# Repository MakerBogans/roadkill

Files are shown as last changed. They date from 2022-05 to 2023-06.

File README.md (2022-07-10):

<div style="text-align: right"><sub>A MakerBogans & Safflower Production</sub></div>


# Roadkill Enhanced Toolhead PCB Family

The RKE family of toolhead boards are based off the roadkill board designed xbst\_ but offers numerous improvements.

- Heater current capacity is greatly improved offering 5A of capacity on the RKE-Long board and 6A on RKE<sup>2</sup>.
- Support for simultaneous use of neopixels, filament sensor, inductive probe and x endstop switch with dedicated ports for all features.
- All boards within the RKE family are pin compatible allowing for mix and matching of boards.

<p align="middle" >
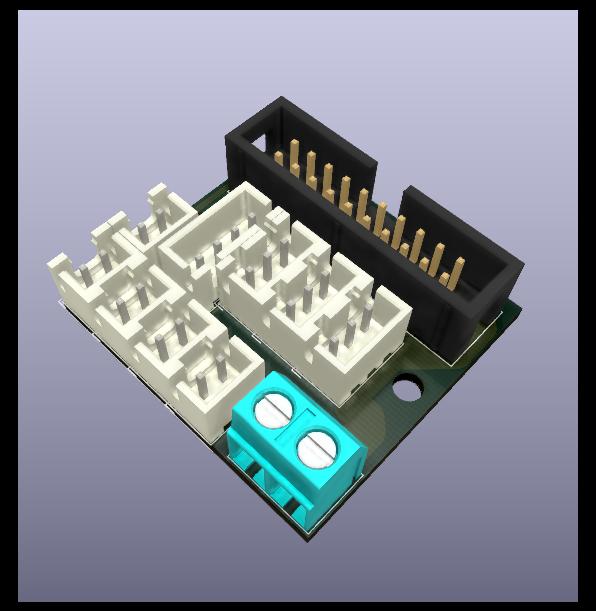
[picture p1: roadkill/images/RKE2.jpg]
  
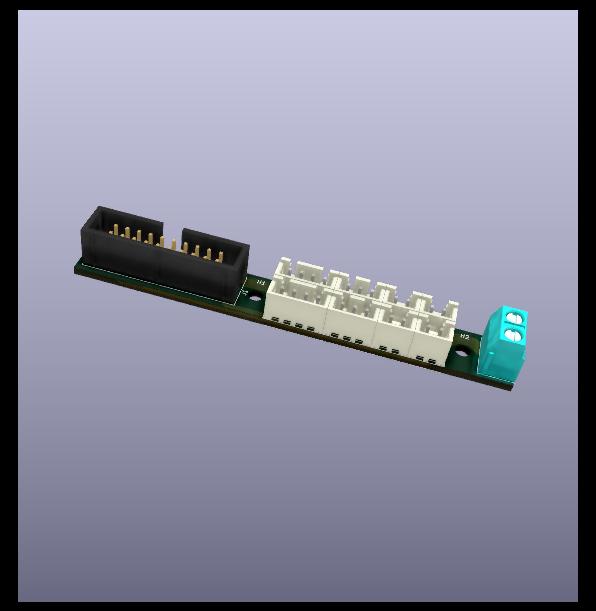
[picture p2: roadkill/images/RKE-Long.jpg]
   
</p>

## Important Notes

- Heater screw terminal is polarised, as the 24V supply is used as a common rail.
- Nylon or printed washers should be used to protect the mounting holes due to the proximity of the traces to the holes.
- LED port is designed for neopixels and uses a common 5V rail with the filament sensor port.
- Probe port has a 24V power rail derived from the heater.

&#9888;<b>Do not connect a wire between the MCU and the Roadkill probe port for V, this will result in backfeeding 24V into the MCU. V is provided from the Heater</b>

## BOM

Per Board,

- 1 x 20 pin IDC header (2x10 2.54mm pitch)
- 5 x 2 pin JST-XH
- 3 x 3 pin JST-XH (2x for RKE Long)
- 1 x 4 pin JST-XH (2X for RKE Long)
- 1 x 5 mm pitch screw terminal (TB00250002BE)

Molex temp-flex ribbon is the preferred ribbon solution (Molex, 100057-0101).

For IDC connector/sockets 3M D89120-0131HK with D3448-89120 strain relief clip are the preferred solutions.

## Pinout for Ports

IDC numbering is ODD_EVEN with 1 denoted by an arrow on the PCB

Pin 1 of the JST-XH ports is the square pads on the PCB.

For RKE<sup>2</sup>

| Port | Pin 1 (IDC PIN)  | Pin 2 (IDC PIN) | Pin 3 (IDC PIN) | Pin 4 (IDC PIN) |
| --- | --- | --- | --- | --- |
| Layer Fan | Fan Voltage (18) | Fan GND (20) | - | - |
| Heater Fan | Fan Voltage (14) | Fan GND (16) | - | - |
| X endstop | GND (2) | Signal (12) | - | - |
| Filament Sensor  | 5 V (4) | GND (2) | Signal (10) | - |
| Neopixel | 5 V (4) | GND (2) | Data In (6) | - |
| Probe | 24 (1,2) | GND (2) | Signal (8) | - |
| Thermistor (T0)  | T0 (11) | GNDA (9) | - | - |
| Extruder Stepper | A1 (19) | A2 (17) | B1 (15) | B2 (13) |
| Heater | 24 V (1,3) | HE GND (5,7) | - | - |

RKE Long utilises a combined Filament Sensor and X endstop port pinout is below.

| Port | Pin 1 (IDC PIN) | Pin 2 (IDC PIN) | Pin 3 (IDC PIN) | Pin 4 (IDC PIN) |
| --- | --- | --- | --- | --- |
| Combined FS and XES | 5 V (4) | GND (2) | Signal (12) | Signal (10) |

# Schematic

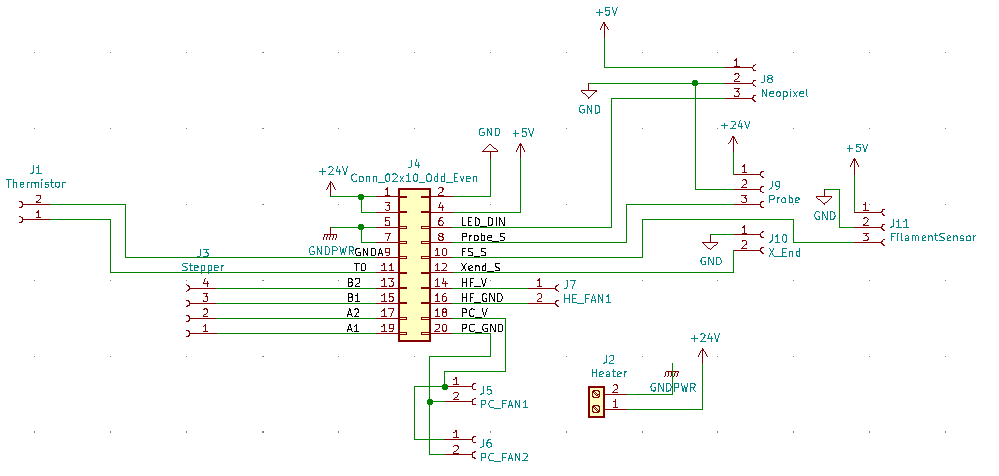
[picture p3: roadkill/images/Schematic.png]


# Probe Wiring
It is critical to wire Z probe correctly to avoid damage to MCU. Follow the below wiring guides

|  |  |
| --- | --- |
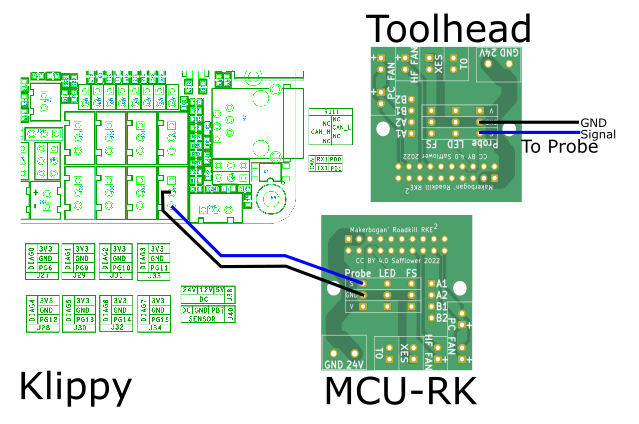
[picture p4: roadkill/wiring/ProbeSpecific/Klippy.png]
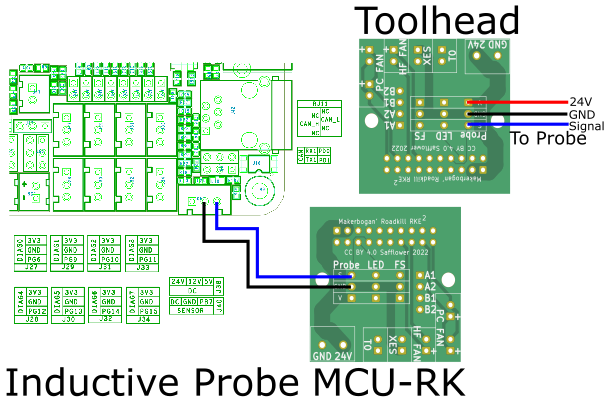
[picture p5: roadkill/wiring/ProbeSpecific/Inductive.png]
|   |  |
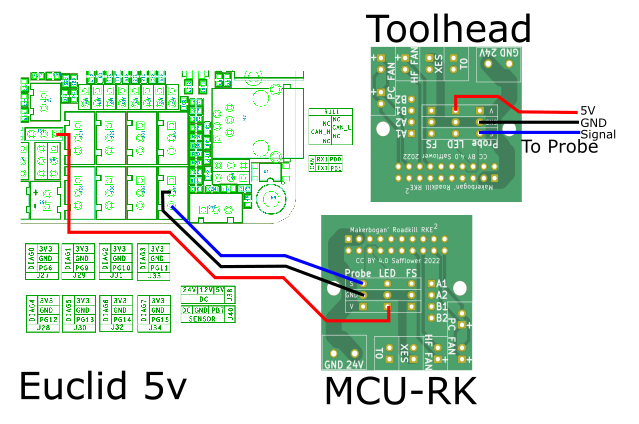
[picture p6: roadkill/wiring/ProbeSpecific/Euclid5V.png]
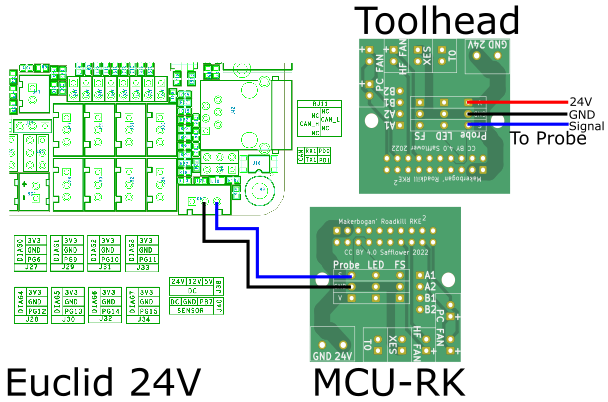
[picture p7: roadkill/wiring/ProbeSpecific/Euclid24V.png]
| |   |

# Troubleshooting

| Number | Symptoms | Cause | Solution |
|---| --- | --- | --- |
| 1 | X endstop is permently triggered or not triggering | X end stop is shorted to GND on the MCU->Roadkill board, S is connected to G on the X endstop port  | Swap X endstop pins on the MCU->Roadkill board |
| 2 | Probe disconnecting when heater is turned  on, Flickering Probe during PWM control of the Probe | Reversed Polarity on the 24 V Screw terminal on the MCU->Roadkill board | Swap  Heater Wires on the MCU->Roadkill board |

# License

<br />This work is licensed under a <a rel="license" href="http://creativecommons.org/licenses/by/4.0/">Creative Commons Attribution 4.0 International License</a>.

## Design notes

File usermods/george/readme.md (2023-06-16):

# Mod description

Another take on the RKE Square mount for the a drive.

Use the pinned version if you have the pinned mod for an easier print.

Can get to the motor mount bolts with use of creative angles.

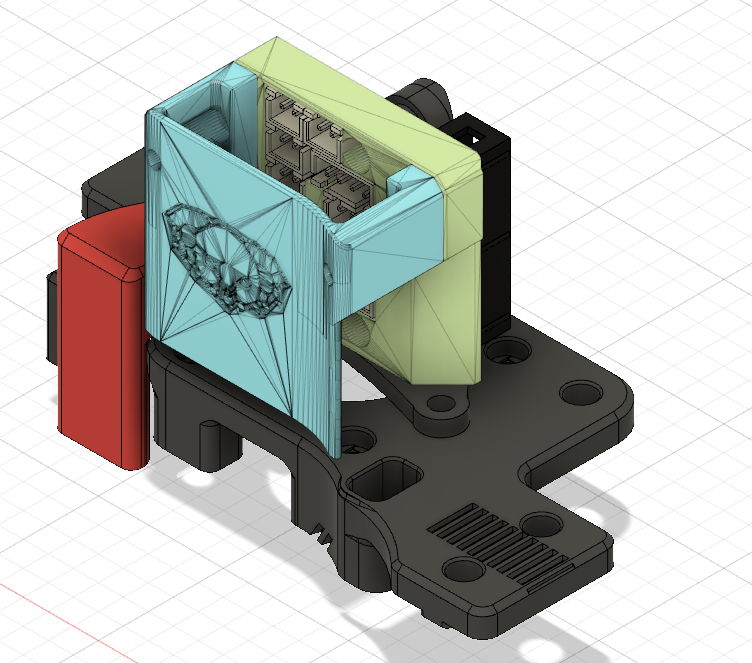
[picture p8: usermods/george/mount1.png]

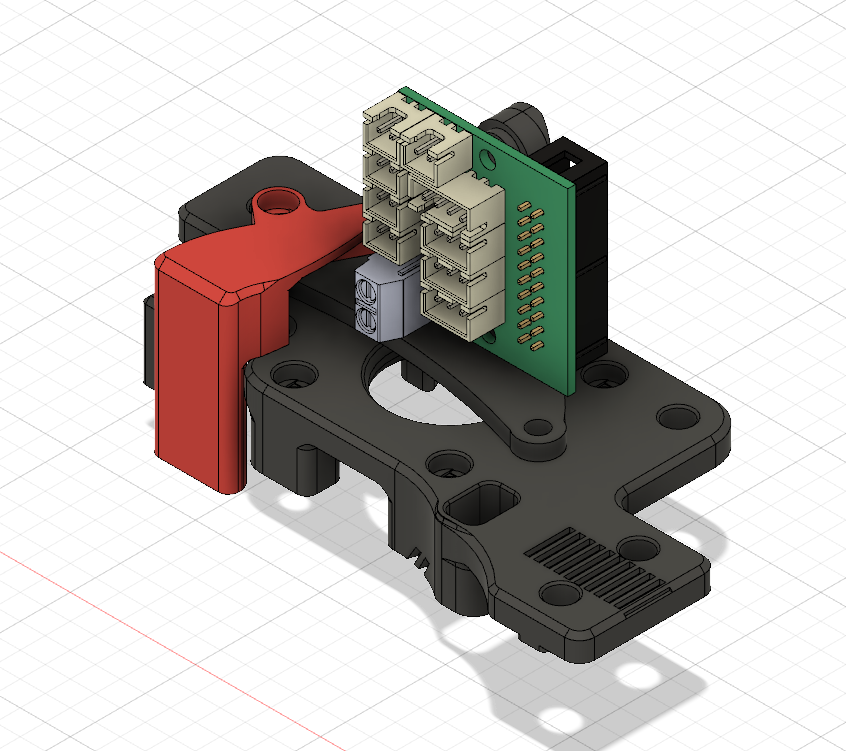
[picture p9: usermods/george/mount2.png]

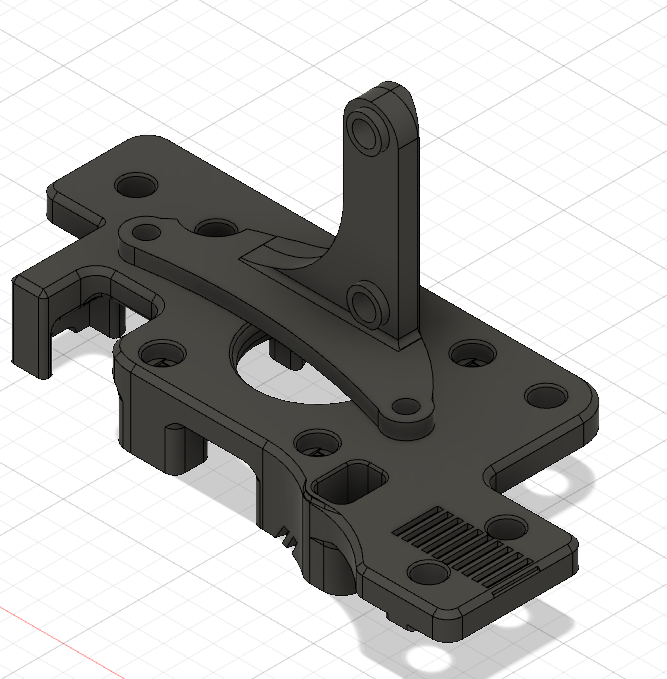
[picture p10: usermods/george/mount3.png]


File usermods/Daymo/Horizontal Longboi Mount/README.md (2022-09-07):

<div style="text-align: right"><sub>A MakerBogans Production</sub></div>


# Horizontal Gantry Mount for RKE Longboi

This mount allows you to use an RKE Longboi on your gantry!

<p align="middle" >
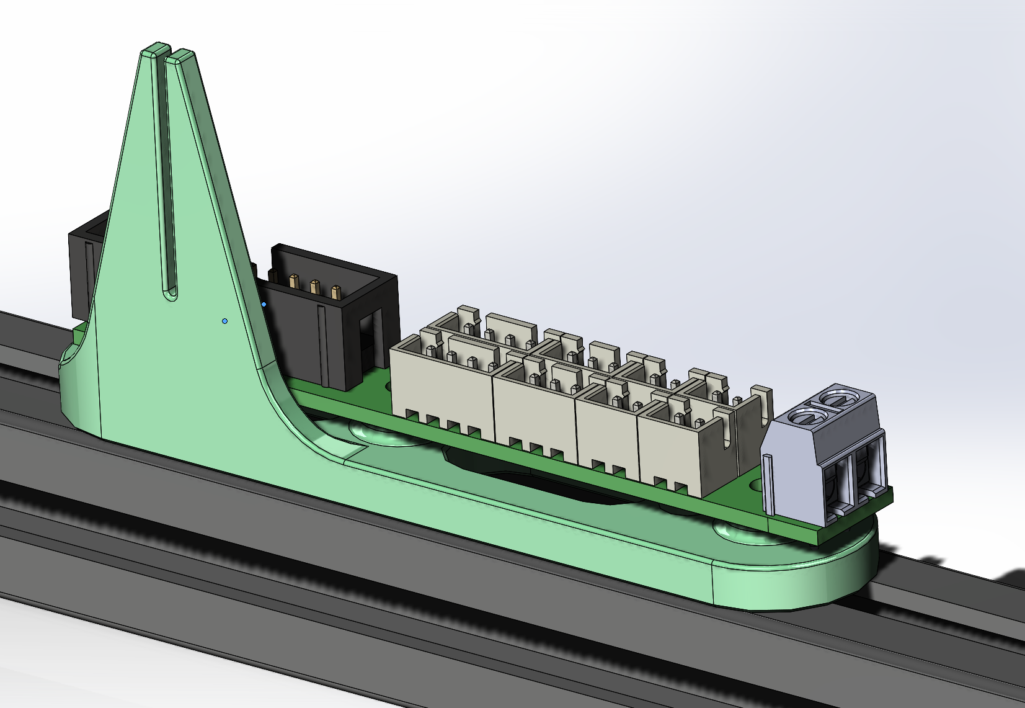
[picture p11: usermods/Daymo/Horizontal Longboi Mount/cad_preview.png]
  
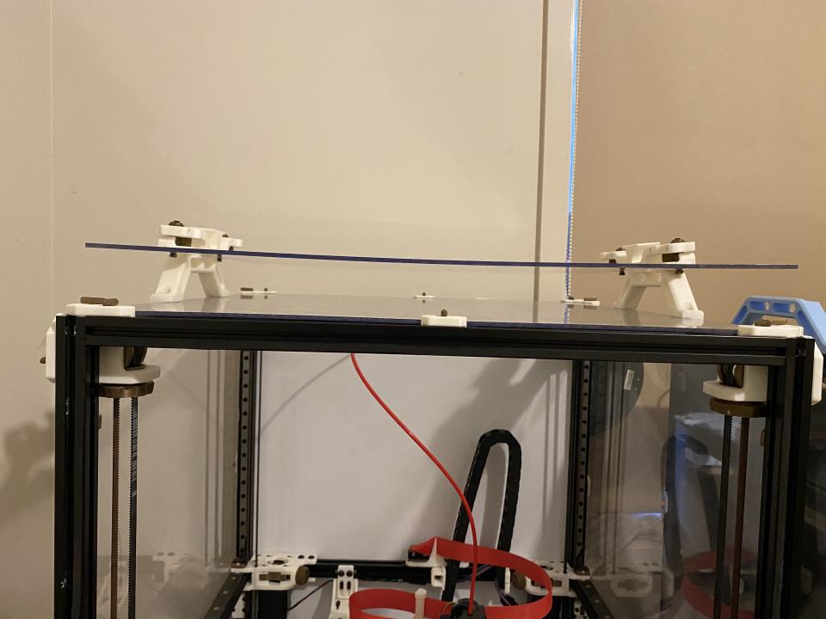
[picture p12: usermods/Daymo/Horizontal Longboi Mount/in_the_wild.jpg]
   
</p>

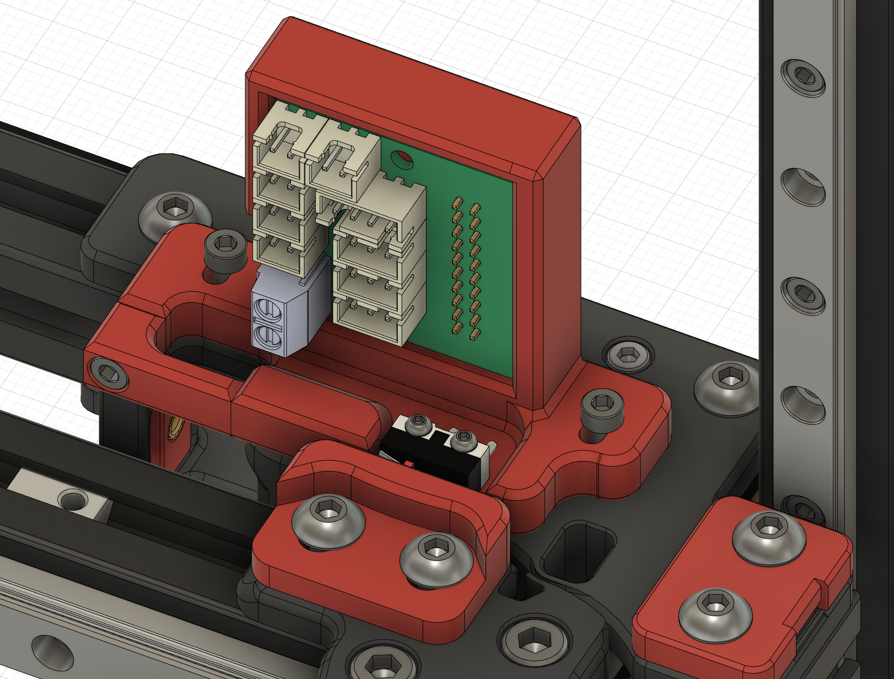
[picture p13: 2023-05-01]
usermods/RedGT500/RKE V2.4 Rear Mount (No Pins Mod)/Pictures/RKE_Mount_05.png

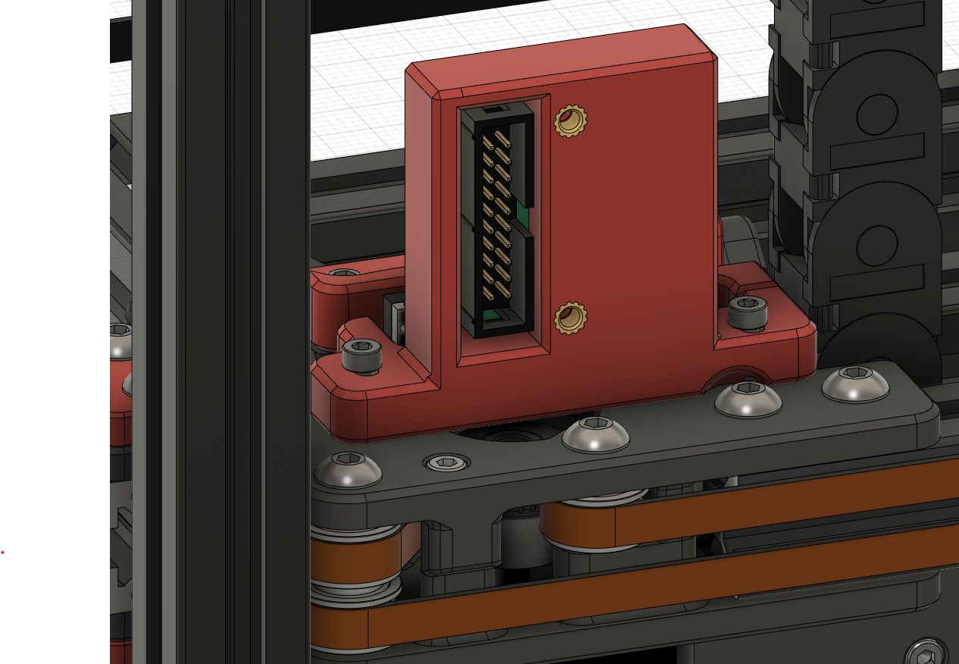
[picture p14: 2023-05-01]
usermods/RedGT500/RKE V2.4 Rear Mount (No Pins Mod)/Pictures/RKE_Mount_03.png

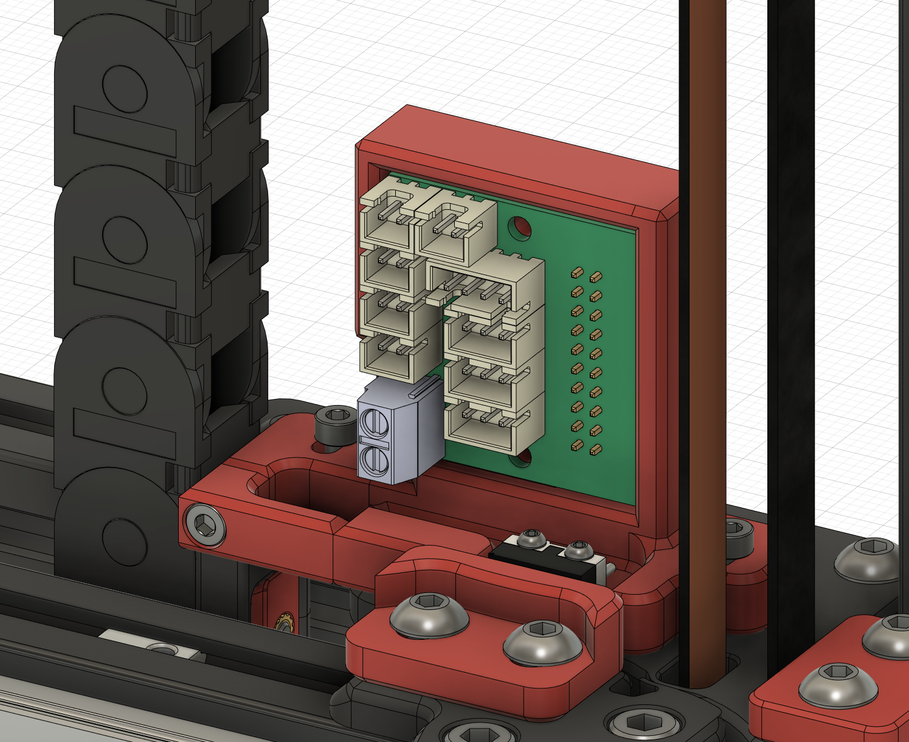
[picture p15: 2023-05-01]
usermods/RedGT500/RKE V2.4 Rear Mount (No Pins Mod)/Pictures/RKE_Mount_02.png

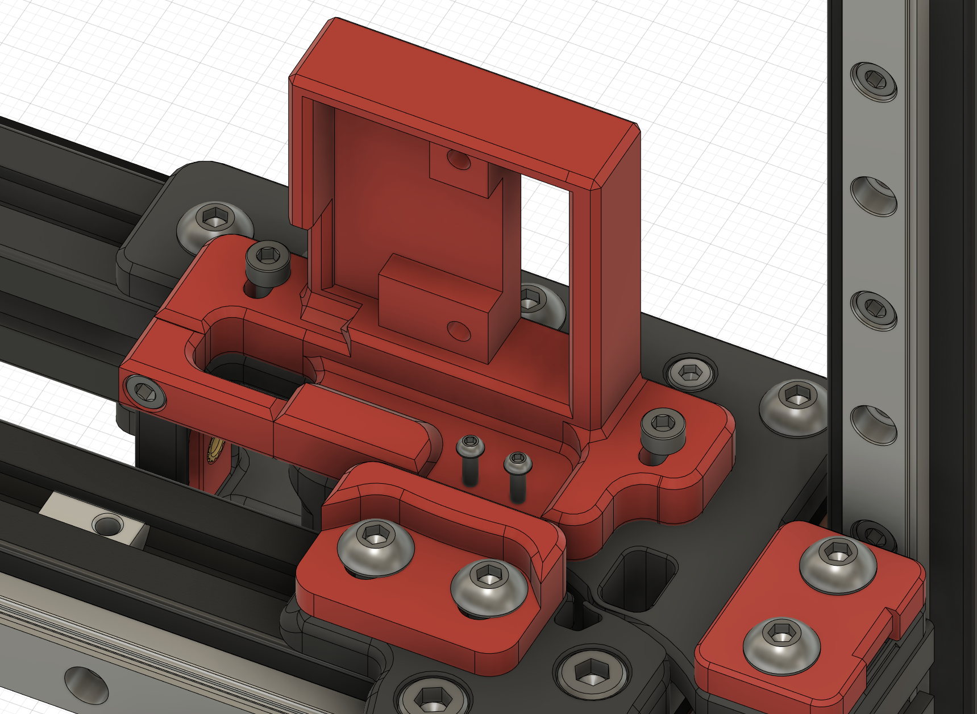
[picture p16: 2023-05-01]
usermods/RedGT500/RKE V2.4 Rear Mount (No Pins Mod)/Pictures/RKE_Mount_06.png

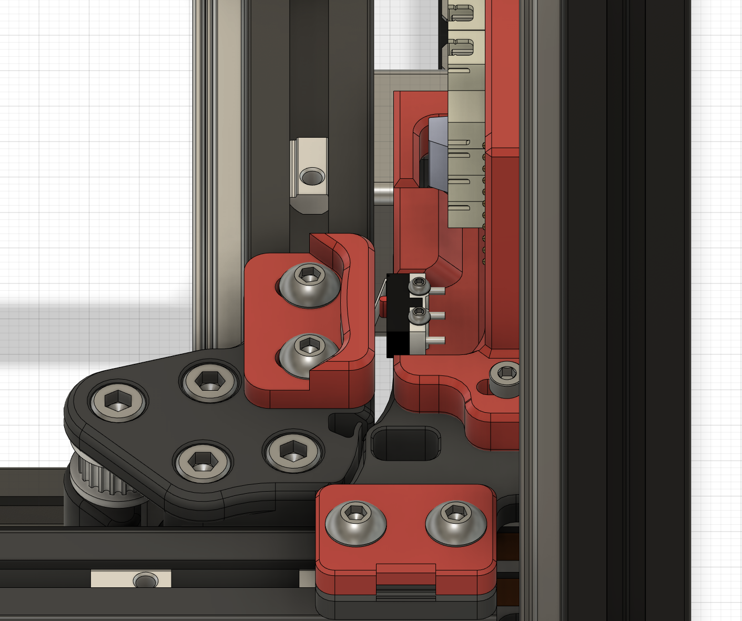
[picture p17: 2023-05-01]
usermods/RedGT500/RKE V2.4 Rear Mount (No Pins Mod)/Pictures/RKE_Mount_04.png

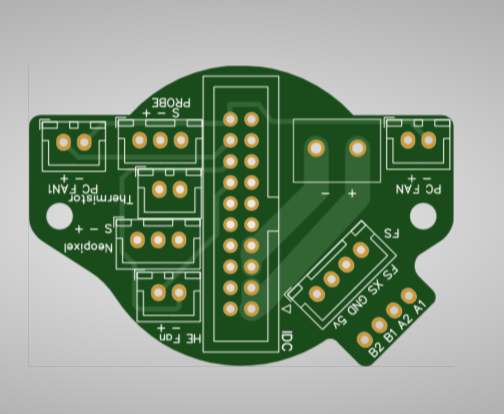
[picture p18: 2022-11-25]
roadkill/images/RK36.png

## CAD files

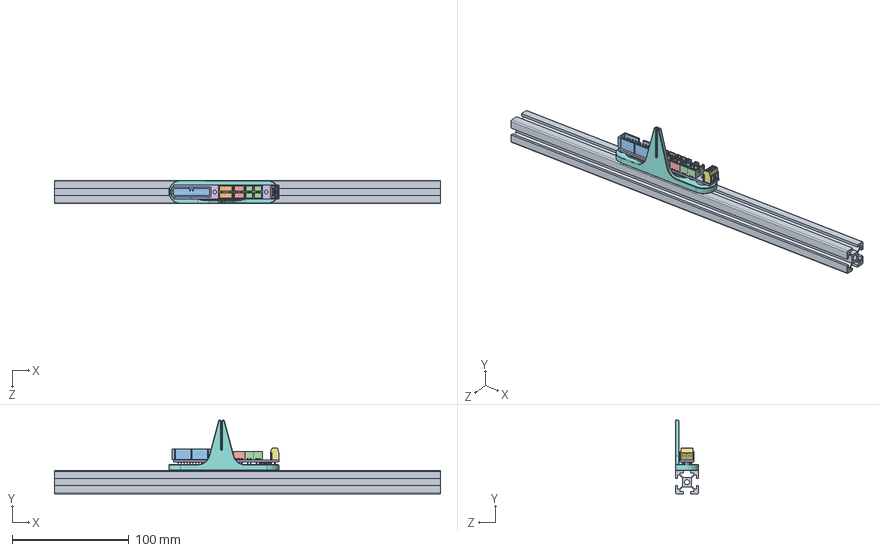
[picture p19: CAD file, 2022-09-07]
usermods/Daymo/Horizontal Longboi Mount/Assem1.SLDASM
330.0 x 63.0 x 20.0 mm
2020 extrusion
SOLID.step x 2
SOLID (1).step
SOLID (2).step x 4
SOLID (3).step x 2
COMPOUND.step
J9_TB002-500-02BE_61F2B5A5.step
Roadkill Horizontal Bracket

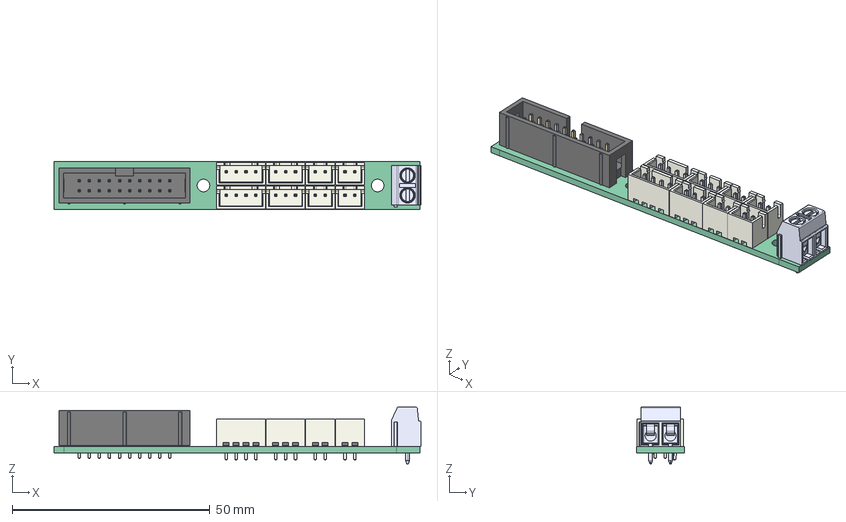
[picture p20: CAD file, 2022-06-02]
roadkill/steps/RKE-Long.step
92.7 x 12.0 x 14.3 mm
Local_CS_704e
Pcb_704e
PCB_Sketch_704e
J1_IDC_Header_2x10_P254mm_Vertical_61F2B46E
J9_TB002-500-02BE_61F2B5A5
J3_JST_B4B_XH_A_61F2B4C2
J11_JST_B2B_XH_A_61F2B5F9
J10_JST_B4B_XH_A_61F2B5D0
J8_JST_B2B_XH_A_61F2B590
J7_JST_B2B_XH_A_61F2B567
J6_JST_B2B_XH_A_61F2B53E
J4_JST_B3B_XH_A_61F2B4EC
J2_JST_B3B_XH_A_61F2B498

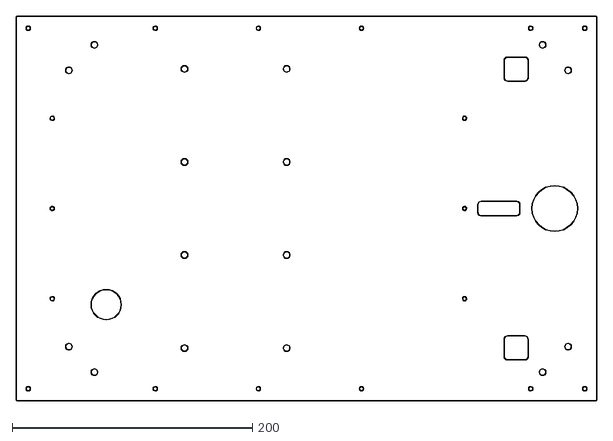
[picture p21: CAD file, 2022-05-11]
usermods/Daymo/Back_Panel_K3/Back_Panel_K3_Roadkill.dxf
483.0 x 320.0

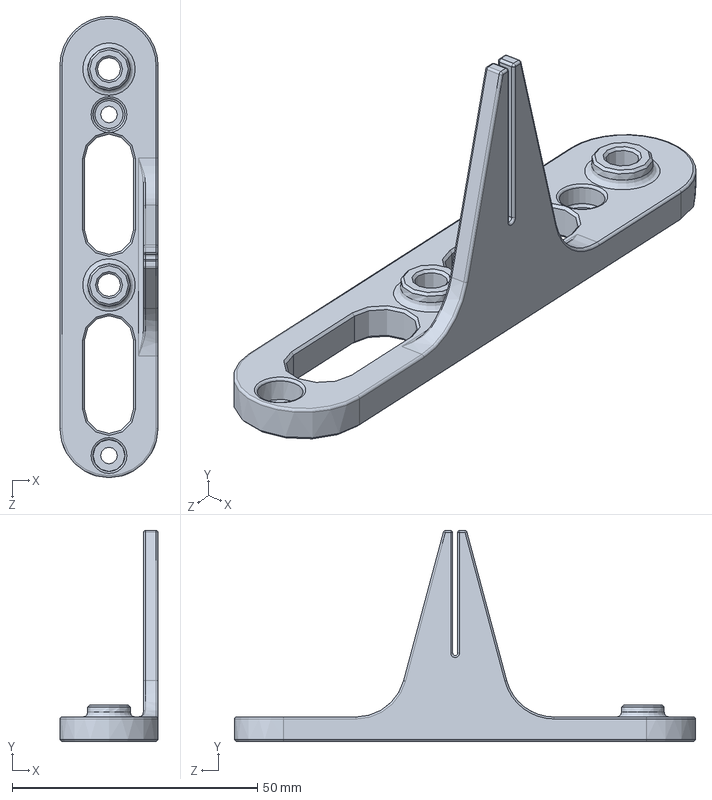
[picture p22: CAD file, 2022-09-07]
usermods/Daymo/Horizontal Longboi Mount/Roadkill Horizontal Bracket.SLDPRT
20.0 x 43.0 x 94.0 mm

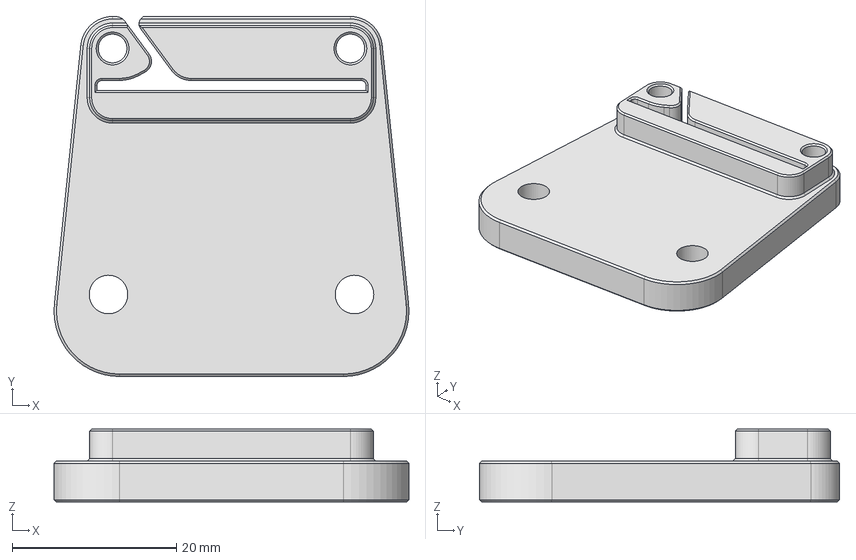
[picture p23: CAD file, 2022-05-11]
usermods/Long/K3 Rear Panel Insert/Rear Panel Insert - Outer - Open - 2mm Panel.step
43.3 x 43.9 x 8.90 mm

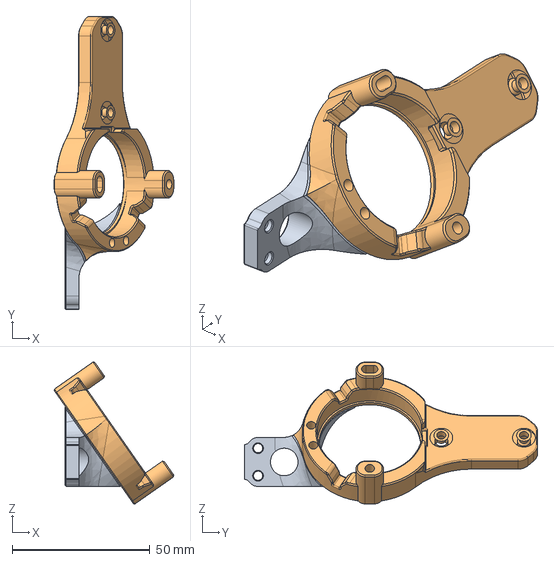
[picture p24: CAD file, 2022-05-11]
usermods/Long/K3 Toolhead Mount/Toolhead Mount - v1.3.step
43.5 x 106.6 x 51.6 mm
Roadkill Mount
Sherpa Mini

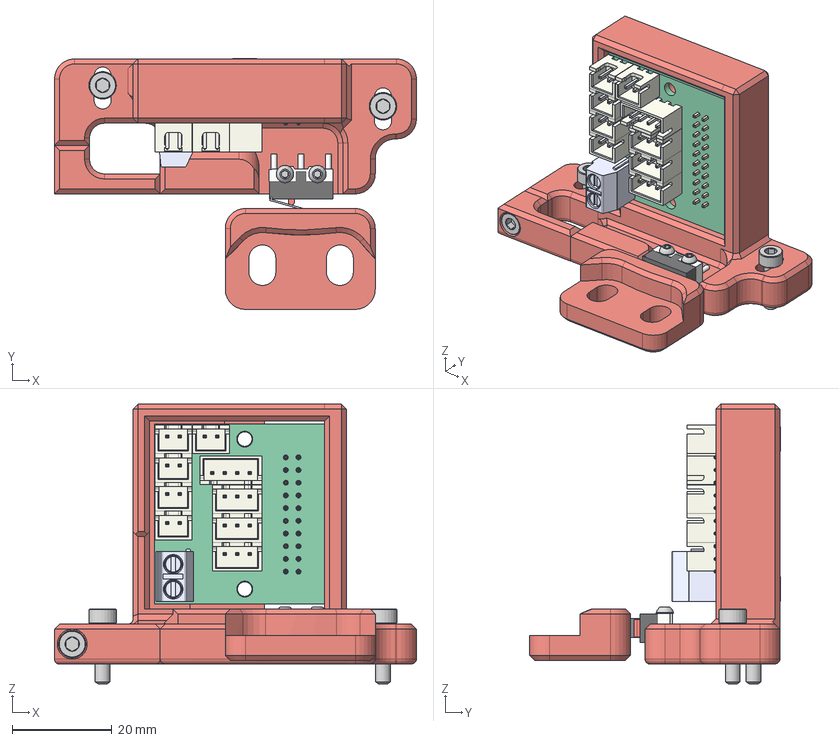
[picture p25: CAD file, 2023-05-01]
usermods/RedGT500/RKE V2.4 Rear Mount (No Pins Mod)/STEP File/Roadkill Gantry Mount BETA v1.step
72.4 x 50.2 x 55.9 mm
KW10 Microswitch (3)
J11_JST_B3B_XH_A_inf
J10_JST_B2B_XH_A_6218E85C
J9_JST_B3B_XH_A_inf
J8_JST_B3B_XH_A_inf
J7_JST_B2B_XH_A_6218E7DF
J6_JST_B2B_XH_A_6218E7B6
J5_JST_B2B_XH_A_6218E78D
J4_IDC_Header_2x10_P254mm_Vertical_inf
J3_JST_B4B_XH_A_6218E72B
J2_TB002-500-02BE_inf
J1_JST_B2B_XH_A_6218E6ED
Pcb_9127
Road Kill A Drive Mount

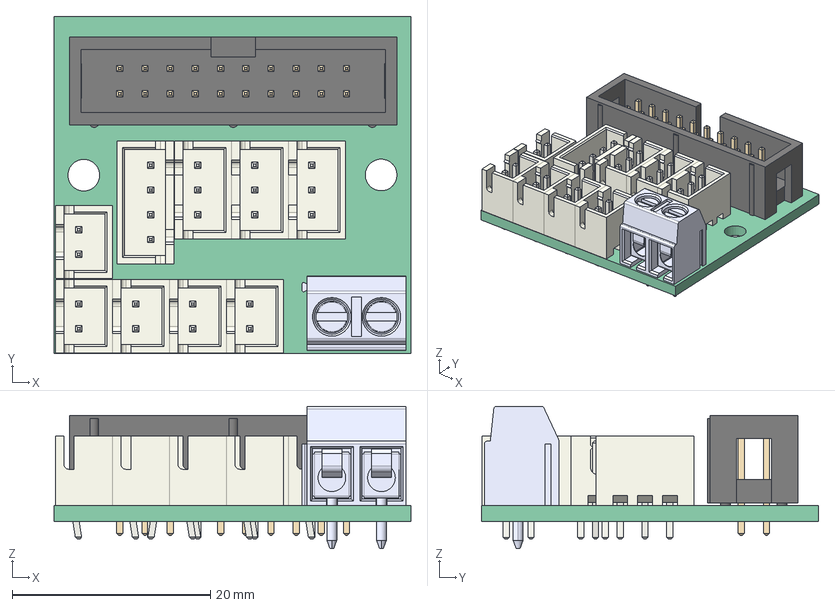
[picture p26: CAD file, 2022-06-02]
roadkill/steps/RKE-SquaredV1.step
36.0 x 34.0 x 14.3 mm
Local_CS_9127
Pcb_9127
PCB_Sketch_9127
J11_JST_B3B_XH_A_inf
J10_JST_B2B_XH_A_6218E85C
J9_JST_B3B_XH_A_inf
J8_JST_B3B_XH_A_inf
J7_JST_B2B_XH_A_6218E7DF
J6_JST_B2B_XH_A_6218E7B6
J5_JST_B2B_XH_A_6218E78D
J4_IDC_Header_2x10_P254mm_Vertical_inf
J3_JST_B4B_XH_A_6218E72B
J2_TB002-500-02BE_inf
J1_JST_B2B_XH_A_6218E6ED

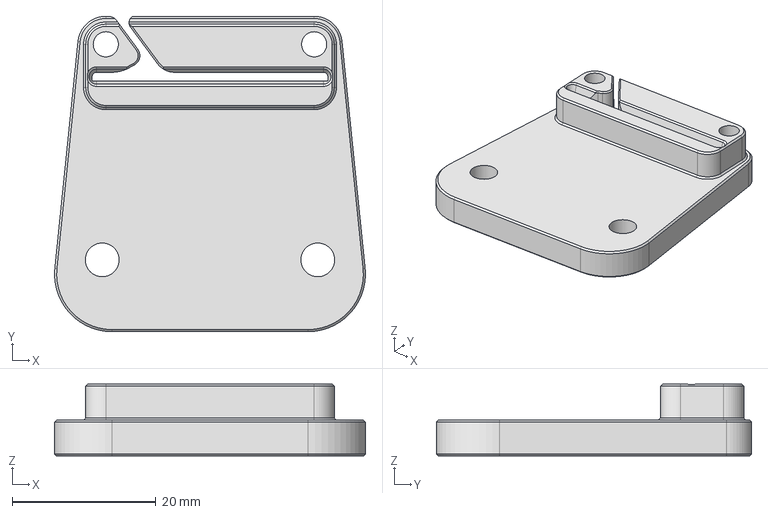
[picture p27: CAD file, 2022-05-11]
usermods/Long/K3 Rear Panel Insert/Rear Panel Insert - Outer - Open - 3mm Panel.step
43.3 x 43.9 x 10.0 mm

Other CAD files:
usermods/Long/K3 Toolhead Mount/Toolhead Mount - Main - Slotted and Pinned - v1.3.stl
usermods/george/RKE A Drive Mount/a_drive_frame_upper_pinned.3mf
usermods/GhettoMat/rk-rearmount.stl
usermods/RedGT500/RKE V2.4 Rear Mount (No Pins Mod)/STL's/Road Kill A Drive Mount.stl
usermods/s1w/rk-shaft-taller.stl
usermods/Usernametaken/Bearing-Shaft/shaft.stl
usermods/george/RKE A Drive Mount/a_drive_frame_upper.3mf
usermods/GhettoMat/rk-cap.stl
usermods/Long/K3 Toolhead Mount/Toolhead Mount - Secondary - Pinned - v1.3.stl
usermods/Daymo/Back_Panel_K3/Back_Panel_K3_Roadkill.dwg
usermods/Daymo/Horizontal Longboi Mount/Roadkill Horizontal Bracket.STL
usermods/GhettoMat/rk-frontmount.f3d
usermods/GhettoMat/rk-frontmount.stl
usermods/GhettoMat/rk-rearmount.f3d
usermods/GhettoMat/rk-shaft.stl
usermods/GhettoMat/rk-xfence.stl
usermods/Long/K3 Rear Panel Insert/Rear Panel Insert - Inner - Open.step
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

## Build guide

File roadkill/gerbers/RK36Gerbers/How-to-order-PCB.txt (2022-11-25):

How to Order PCB

Please refer to:
https://docs.easyeda.com/en/PCB/Order-PCB

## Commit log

2022-05-10 Initial import for Roadkill files
    [RKE-Long.step, RKE-SquaredV1.step]
2022-05-11 Import some mods
    [Back_Panel_K3_Roadkill.dwg, Back_Panel_K3_Roadkill.dxf, Rear Panel Insert - Inner - Open.step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]
2022-06-01 fix LFS file issue
    [RKE-Long.step, RKE-SquaredV1.step]
2022-07-06 Probe Wiring Guides
2022-09-02 Add GhettoMats swivels
    [rk-cap.stl, rk-frontmount.f3d, rk-frontmount.stl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]
2022-09-04 Adding horizontal longboi mount
    [Assem1.SLDASM, Roadkill Horizontal Bracket.SLDPRT, Roadkill Horizontal Bracket.STL]
2022-11-25 Added the Noctus RK36 gerbers
    [Drill_NPTH_Through.DRL, Drill_PTH_Through.DRL, Drill_PTH_Through_Via.DRL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]
2023-04-06 more mods
    [bearing-shaft.f3d, cap.stl, mount.stl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]
2023-05-01 RKE V2.4 Rear Mount and Y Endstop Bracket
    RKE Mount for the "A" drive gantry bracket on the V2.4. Incorporates relocated "Y" endstop and is adjustable to set correct homing location.
    [Road Kill A Drive Mount.stl, Roadkill Gantry Mount BETA v1.step, Wire Cover.stl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]
